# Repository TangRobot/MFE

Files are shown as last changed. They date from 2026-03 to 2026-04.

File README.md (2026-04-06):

# MFE: Multimodal Hand Exoskeleton

This is the official open-source repository for the paper:

**MFE: A Multimodal Hand Exoskeleton With Interactive Force, Pressure and Thermo-Haptic Feedback**

📄 [Read the Paper](http://arxiv.org/abs/2604.02820)

---

## Hardware

### Hand Exoskeleton (Canonical Version)

#### BOM

| Item | Specification | Quantity | Notes | Link |
|---|---|---|---|---|
| 3D Printed Parts | See `Hardware/Hand_Exoskeleton_CAD` | 1 set | Print each file once | - |
| Dynamixel Servos | XL-330-M288-T | 5 | with cables & screws | https://en.robotis.com/shop_en/item.php?it_id=902-0163-000 |
| U2D2 Hub | - | 1 | - | https://en.robotis.com/shop_en/item.php?it_id=902-0132-000 |
| U2D2 PHB Set | - | 1 | - | https://en.robotis.com/shop_en/item.php?it_id=902-0145-001 |
| DC Power Supply | 5V | 1 | - | - |
| Screws | M3 × 6 mm | 2 | - | - |
| Screws | M3 × 8 mm | 3 | - | - |
| Screws | M3 × 16 mm | 15 | - | - |
| Lock Nuts | M3 anti-slip | 15 | - | - |
| Heat-set Inserts | M3 × 3 mm (height) × 4.2 mm (OD) | 2 | - | - |
| EVA Foam | 10 cm × 10 cm | 1 | Recommended: 2 mm thickness, Shore hardness 30A | - |
| Velcro Straps (Wide) | 40 cm (length) × 20 mm (width) | 2 | For hand fixation | https://e.tb.cn/h.ih3Ne5haJRBw5nE?tk=OanP5ZXM8IF |
| Velcro Straps (Narrow) | 8 cm (length) × 5 mm (width) | Several | Optional for fingertip fixation | https://e.tb.cn/h.i6odaRXD7jrzqni?tk=6yex5ZX9u82 |

#### 3D Printing Requirements

To print all required parts, you will need:

- 3D printer (0.4 mm nozzle)
- PLA filament (1 spool)
- TPU 95A filament (1 spool)

### Assembly Instructions

0. Before starting the assembly process, configure all Dynamixel servos by assigning their IDs, setting the baud rate, and verifying that each servo operates correctly. Determine the correspondence between each servo and finger in advance.

1. Print all structural components from the directory `Hardware/Hand_Exoskeleton_CAD`, ensuring that you print each file once. For PLA parts, use at least four wall layers and 30% infill, and organize finger linkage components separately to avoid confusion. For TPU 95A parts, use 100% infill, and orient the fingertip sleeves so that the smaller opening faces the print bed.

2. Use a soldering iron to embed two heat-set inserts into the side holes of the lower base component.

3. Assemble the five finger linkages using M3 × 16 mm screws and M3 lock nuts, and adjust the screw tightness so that each joint rotates freely without resistance.

4. Attach the distal ends of each linkage to the servo horns using the longer screws provided in the Dynamixel kit.

5. Mount the servos and corresponding linkages onto the base structure as follows: attach the index and ring fingers to the upper base, attach the middle and little fingers to the lower base, and attach the thumb to the side base. Ensure correct ordering and alignment during installation.

6. Connect the servos in pairs using Dynamixel cables by pairing the index with the ring finger servos and the middle with the little finger servos.

7. Assemble the upper and lower base structures using M3 × 8 mm screws.

8. Attach the side base to the lower base using M3 × 6 mm screws.

9. Connect all servos using Dynamixel cables and link them to the U2D2 Hub.

10. Cut the EVA foam into an appropriate shape and attach it to the surface of the lower base that contacts the back of the hand.

11. Use wide Velcro straps to secure the exoskeleton onto the back of the hand.

12. Use narrow Velcro straps to further secure the fingertip sleeves if necessary.

---

## Software

### Installation

The Dynamixel SDK can be installed using the following command:

```bash
pip install dynamixel_sdk
```

### Usage

Please refer to the [Official Dynamixel SDK Documentation](https://emanual.robotis.com/docs/en/software/dynamixel/dynamixel_sdk/download/) and our [paper](http://arxiv.org/abs/2604.02820) for logic on reading encoder positions and setting force feedback intensity.

A simple implementation example is provided in `Software/MFE_control.py`, which demonstrates force feedback control between the hand exoskeleton and the Inspire RH56BFX robotic hand (both for right hand). Please follow the TODO comments to adapt it to your device, or extend this implementation to develop control logic for other robotic hands.

---

## Citation

If you use this repository in your research, please cite:

```bash
@ARTICLE{Tang2026MFE,
  author={Tang, Ziyuan and Guo, Yitian and Xiao, Chenxi},
  journal={IEEE Robotics and Automation Letters}, 
  title={MFE: A Multimodal Hand Exoskeleton With Interactive Force, Pressure and Thermo-Haptic Feedback}, 
  year={2026},
  volume={11},
  number={3},
  pages={3756-3763},
  doi={10.1109/LRA.2026.3662616}}
```

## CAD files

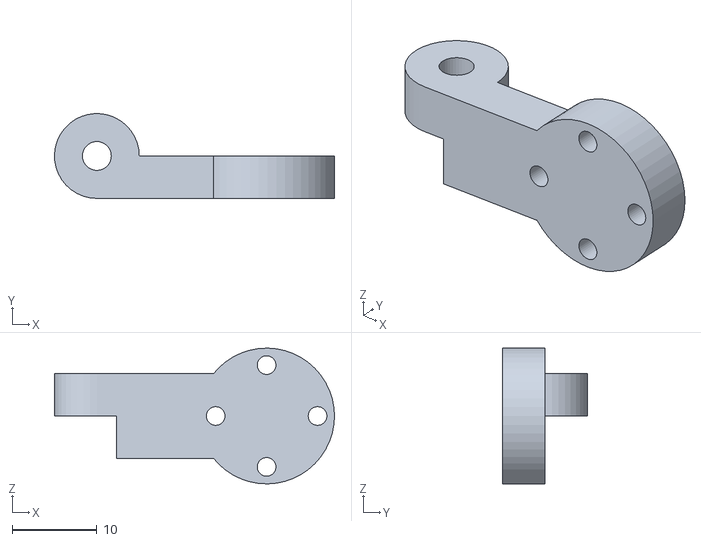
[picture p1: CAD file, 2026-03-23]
Hardware/Hand_Exoskeleton_CAD/PLA/middle_link3.STL
33.0 x 9.99 x 16.0

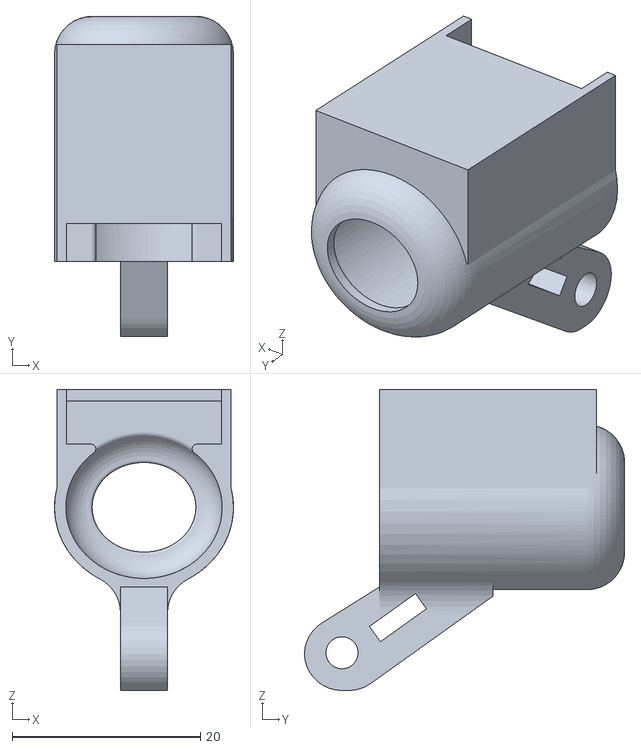
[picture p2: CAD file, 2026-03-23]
Hardware/Hand_Exoskeleton_CAD/TPU/index_sleeve.STL
19.0 x 34.0 x 31.9

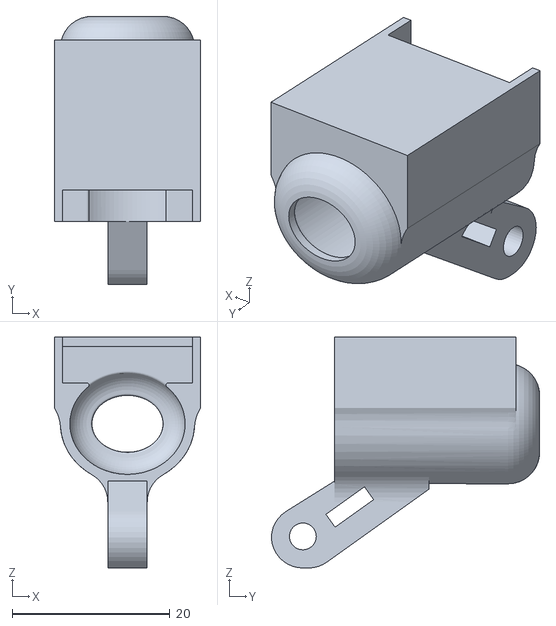
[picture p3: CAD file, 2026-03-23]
Hardware/Hand_Exoskeleton_CAD/TPU/little_sleeve.STL
18.5 x 34.0 x 29.3

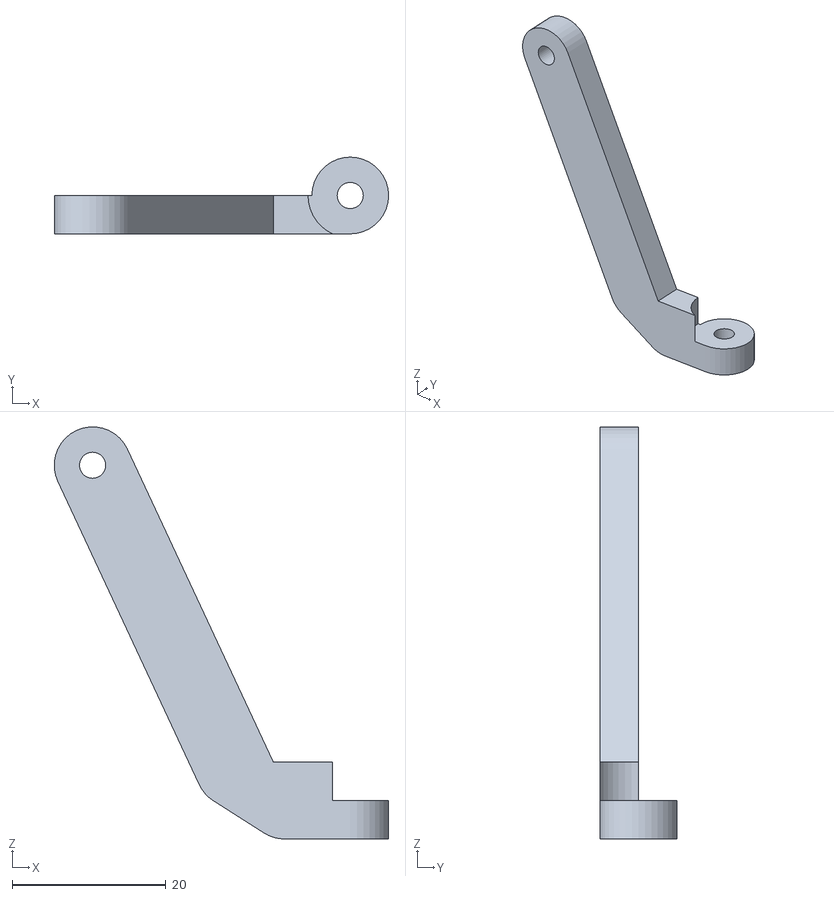
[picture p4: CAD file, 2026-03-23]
Hardware/Hand_Exoskeleton_CAD/PLA/thumb_link2.STL
43.5 x 10.0 x 53.7

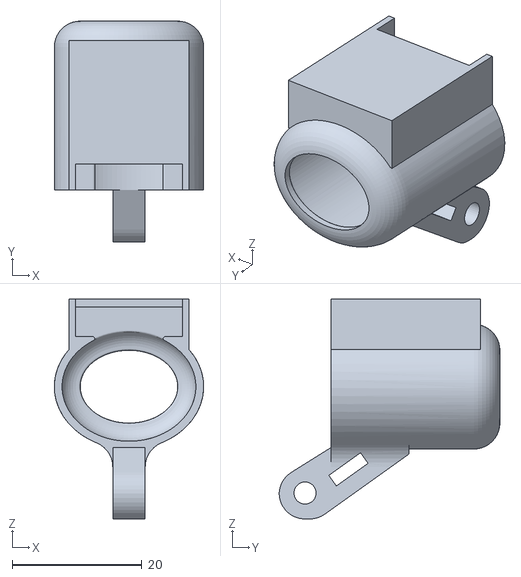
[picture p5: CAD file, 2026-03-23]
Hardware/Hand_Exoskeleton_CAD/TPU/thumb_sleeve.STL
23.0 x 34.0 x 33.9

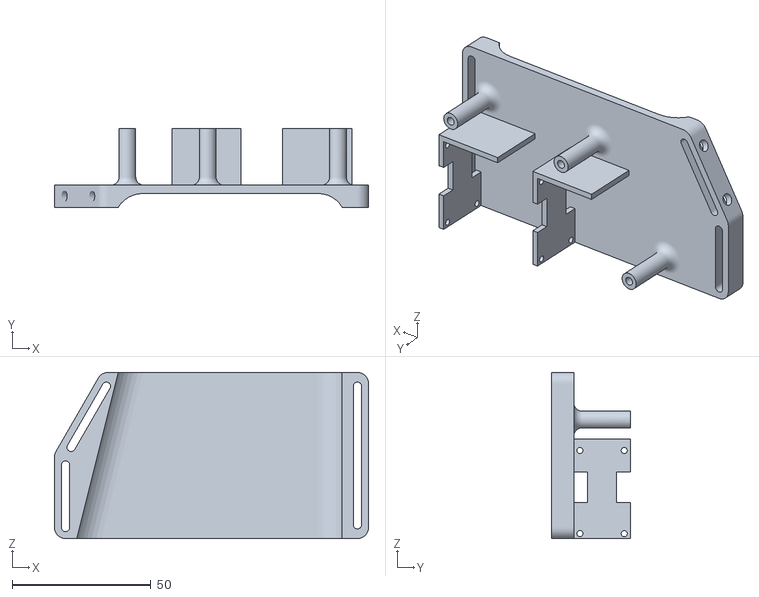
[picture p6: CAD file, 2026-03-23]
Hardware/Hand_Exoskeleton_CAD/PLA/lower_base.STL
113.3 x 28.4 x 60.0

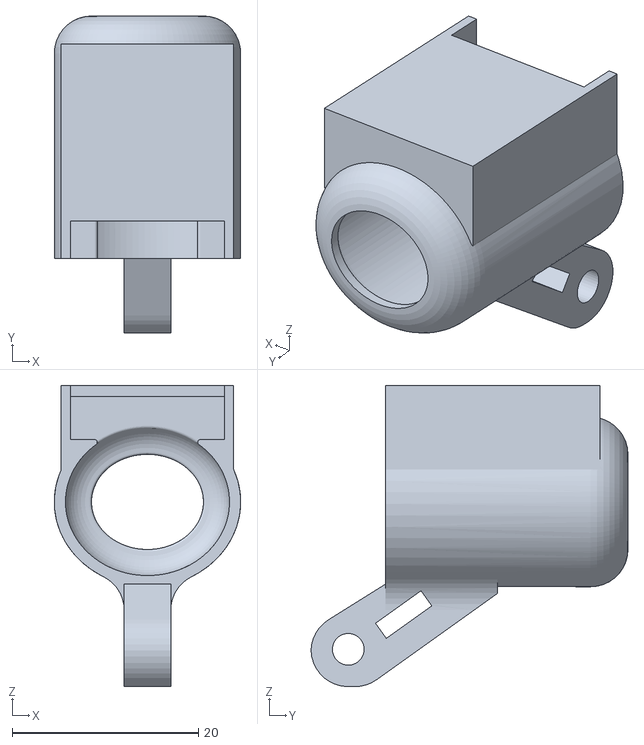
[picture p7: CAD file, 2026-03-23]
Hardware/Hand_Exoskeleton_CAD/TPU/middle_sleeve.STL
20.0 x 34.0 x 32.3

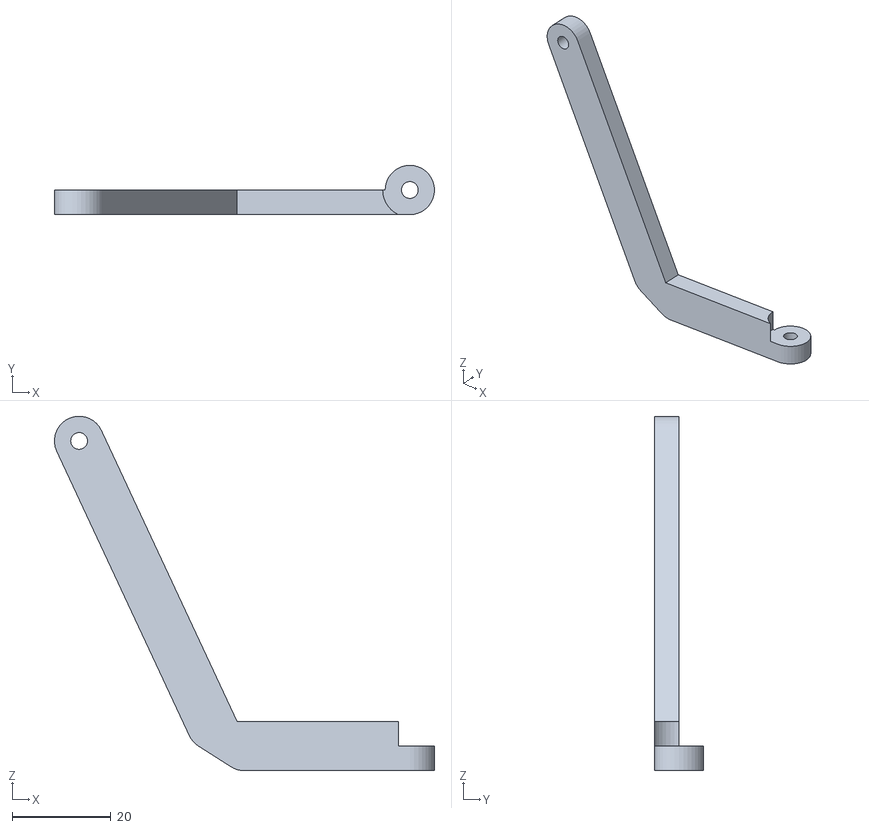
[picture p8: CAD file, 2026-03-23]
Hardware/Hand_Exoskeleton_CAD/PLA/middle_link2.STL
77.0 x 10.0 x 71.8

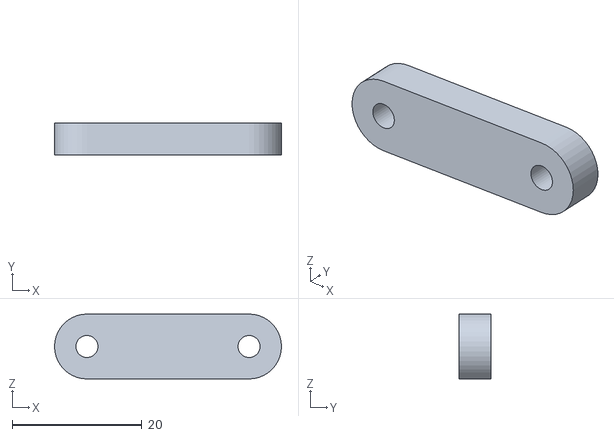
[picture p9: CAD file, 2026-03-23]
Hardware/Hand_Exoskeleton_CAD/PLA/thumb_link1.STL
35.0 x 5.00 x 10.0

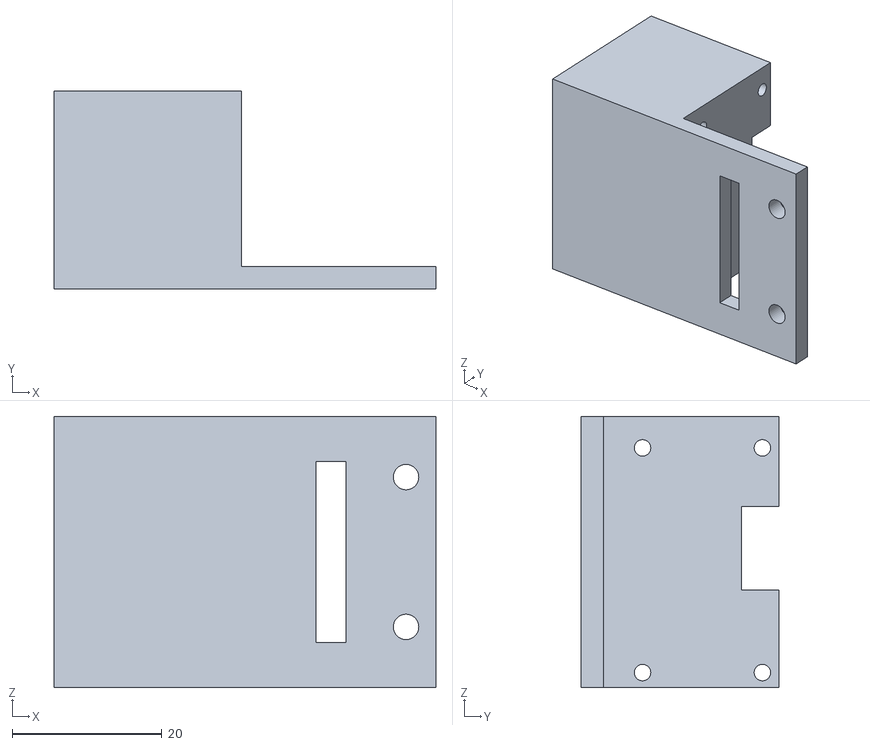
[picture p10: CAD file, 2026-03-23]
Hardware/Hand_Exoskeleton_CAD/PLA/side_base.STL
51.0 x 26.4 x 36.2

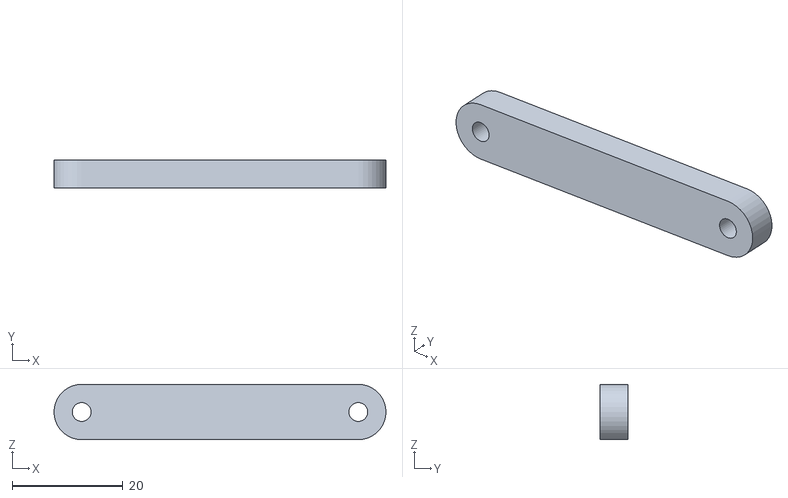
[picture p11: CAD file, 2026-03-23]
Hardware/Hand_Exoskeleton_CAD/PLA/ring_link1.STL
60.0 x 5.00 x 10.0

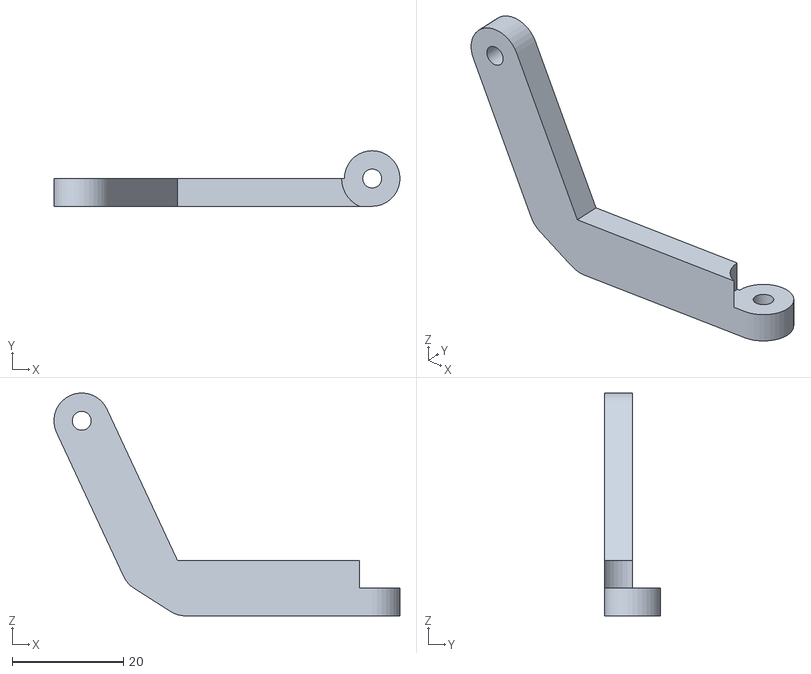
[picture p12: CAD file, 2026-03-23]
Hardware/Hand_Exoskeleton_CAD/PLA/little_link2.STL
62.2 x 10.0 x 40.1

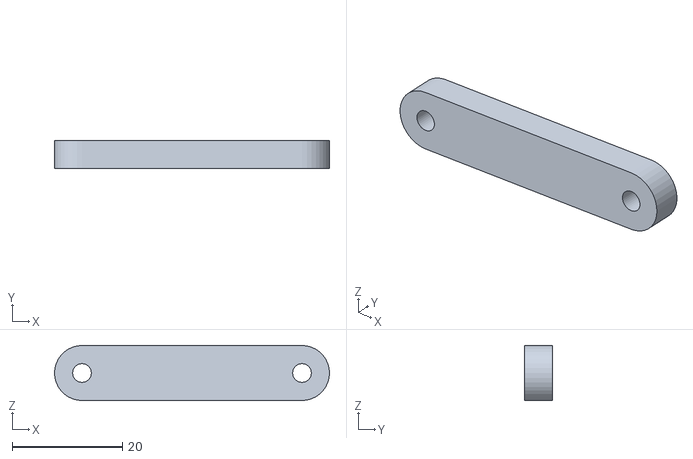
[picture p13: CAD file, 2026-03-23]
Hardware/Hand_Exoskeleton_CAD/PLA/little_link1.STL
50.0 x 5.00 x 10.0

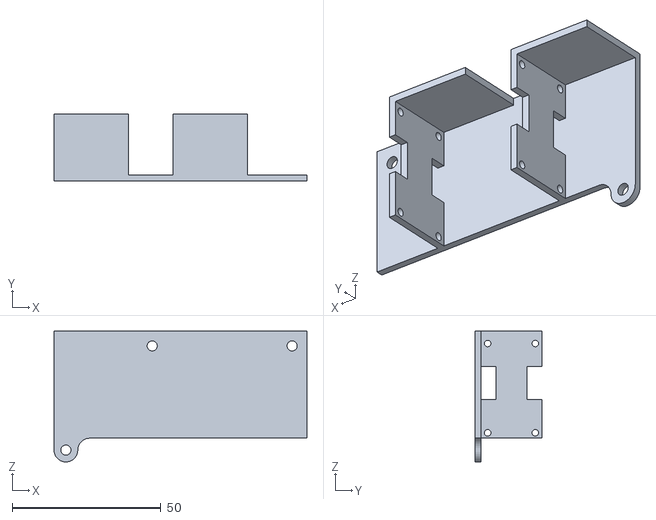
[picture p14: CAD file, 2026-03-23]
Hardware/Hand_Exoskeleton_CAD/PLA/upper_base.STL
85.0 x 22.4 x 44.0

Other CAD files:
Hardware/Hand_Exoskeleton_CAD/TPU/ring_sleeve.STL
Hardware/Hand_Exoskeleton_CAD/PLA/index_link1.STL
Hardware/Hand_Exoskeleton_CAD/PLA/index_link2.STL
Hardware/Hand_Exoskeleton_CAD/PLA/middle_link1.STL
Hardware/Hand_Exoskeleton_CAD/PLA/ring_link2.STL

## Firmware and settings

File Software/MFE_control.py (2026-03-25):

"""
This file is part of the official implementation for the paper:
"MFE: A Multimodal Hand Exoskeleton With Interactive Force, Pressure and Thermo-Haptic Feedback".
DOI: 10.1109/LRA.2026.3662616

This script provides basic functionalities for communicating with Hand Exoskeleton,
including state reading and control command execution, and serves as a reference
implementation for the force feedback control in the MFE system.

The code is intended as a minimal and adaptable example. Users should modify and
extend it according to their specific hardware setup and experimental requirements.

Please adapt this code to your own device by following the TODO comments in the file.
In particular, make sure to configure parameters such as:
- Serial port name
- Baud rate
- Servo IDs
- Control mode and limits
- Dex hand control logic

Refer to the official Dynamixel SDK documentation for detailed usage instructions.

If you use this code in your research, please cite the corresponding paper.

This project is released under the MIT License.
"""

import os
import numpy as np
from pymodbus import FramerType
from pymodbus.client import ModbusSerialClient
from dynamixel_sdk import *

# ------------------- Configuration Section -------------------

ADDR_TORQUE_ENABLE          = 64
ADDR_GOAL_POSITION          = 116
ADDR_PRESENT_POSITION       = 132
ADDR_DRIVE_MODE             = 11
ADDR_GOAL_CURRENT           = 102
TORQUE_ENABLE               = 1
TORQUE_DISABLE              = 0
DRIVE_MODE_CURRENT          = 0

# TODO: Configure these parameters according to your Dynamixel servo setup.
DXL_ID = [1, 2, 3, 4, 5] #From thumb to little finger.
DEVICENAME = 'COM1'
BAUDRATE = 115200
PROTOCOL_VERSION = 2.0
# TODO: Configure these parameters according to your Inspire hand setup,
# or implement your own hand control logic if you are using a different dex hand.
HAND_PORT = 'COM2'
HAND_BAUDRATE = 115200

# ------------------- Utility Functions -------------------

def getch():
    if os.name == 'nt':
        import msvcrt
        return msvcrt.getch().decode()
    else:
        import sys, tty, termios
        fd = sys.stdin.fileno()
        old_settings = termios.tcgetattr(fd)
        try:
            tty.setraw(fd)
            ch = sys.stdin.read(1)
        finally:
            termios.tcsetattr(fd, termios.TCSADRAIN, old_settings)
        return ch

def check(dxl_comm_result, dxl_error, packetHandler):
    if dxl_comm_result != COMM_SUCCESS:
        print(packetHandler.getTxRxResult(dxl_comm_result))
    elif dxl_error != 0:
        print(packetHandler.getRxPacketError(dxl_error))

# ------------------- Inspire Hand Control -------------------
# TODO: Implement your own hand control logic if you are using a different dex hand.
def create_modbus_client():
    client = ModbusSerialClient(
        framer=FramerType.RTU,
        port=HAND_PORT,
        baudrate=HAND_BAUDRATE,
        timeout=1,
        stopbits=1,
        bytesize=8,
        parity='N'
    )
    if not client.connect():
        raise RuntimeError('Unable to connect to Modbus RTU server.')
    return client

def write_single_register(client, hand_id, reg_addr, regval_int16):
    result = client.write_register(reg_addr, regval_int16, device_id=hand_id)
    return result.isError(), result

def write_multiple_registers(client, hand_id, reg_addr, values):
    result = client.write_registers(reg_addr, values, device_id=hand_id)
    return result.isError(), result

def read_register(client, hand_id, reg_addr, num_int16_regs=6, dtype=np.int16):
    result = client.read_holding_registers(reg_addr, count=num_int16_regs, device_id=hand_id)
    if result.isError():
        return []
    registers = result.registers
    results = []
    for val in registers:
        if dtype in (np.int16, np.uint16):
            results.append(np.array(val))
        elif dtype in (np.int8, np.uint8):
            results.append(np.array(val & 0xff))
            results.append(np.array((val >> 8) & 0xff))
        else:
            results.append(np.array(val))
    return np.array(results).astype(dtype)

class InspireHand:
    def __init__(self, client, hand_id):
        self.client = client
        self.hand_id = hand_id
    def set_pos(self, pos, index=None):
        if index is not None:
            if not 0 <= index <= 5:
                return False, 'Index out of range'
            reg_addr = 0x05C2 + index * 2
            return write_single_register(self.client, self.hand_id, reg_addr, pos)
        if len(pos) != 6:
            return False, None
        reg_addr = 0x05C2
        return write_multiple_registers(self.client, self.hand_id, reg_addr, pos)
    def set_force(self, force, index=None):
        if index is not None:
            if not 0 <= index <= 5:
                return False, 'Index out of range'
            reg_addr = 0x05DA + index * 2
            return write_single_register(self.client, self.hand_id, reg_addr, force)
        if len(force) != 6:
            return False, None
        reg_addr = 0x05DA
        return write_multiple_registers(self.client, self.hand_id, reg_addr, force)
    def read_force(self):
        reg_addr = 0x062E
        return read_register(self.client, self.hand_id, reg_addr, num_int16_regs=6)

# ------------------- Dynamixel Servo Control -------------------

def setup_dynamixel():
    portHandler = PortHandler(DEVICENAME)
    packetHandler = PacketHandler(PROTOCOL_VERSION)
    if not portHandler.openPort():
        raise RuntimeError('Failed to open the port')
    if not portHandler.setBaudRate(BAUDRATE):
        raise RuntimeError('Failed to set baudrate')
    return portHandler, packetHandler

# ------------------- Main Control Logic -------------------

def main():
    # Initialize hardware
    # TODO: Implement your own initialization logic if you are using a different dex hand.
    client = create_modbus_client()
    hand = InspireHand(client, hand_id=0x01)
    portHandler, packetHandler = setup_dynamixel()
    initial_position = [0] * 5
    longest_position = [0] * 5
    finger_position = [0] * 5
    goal_current = [0] * 5
    # Disable torque for all servos
    for i in DXL_ID:
        dxl_comm_result, dxl_error = packetHandler.write1ByteTxRx(portHandler, i, ADDR_TORQUE_ENABLE, TORQUE_DISABLE)
        check(dxl_comm_result, dxl_error, packetHandler)
    # Set initial positions based on user input
    print('Bend your thumb and press any key to set initial position.')
    getch()
    i = DXL_ID[0]
    longest_position[0], dxl_comm_result, dxl_error = packetHandler.read4ByteTxRx(portHandler, i, ADDR_PRESENT_POSITION)
    check(dxl_comm_result, dxl_error, packetHandler)
    print('Extend your thumb straight and press any key to set initial position.')
    getch()
    initial_position[0], dxl_comm_result, dxl_error = packetHandler.read4ByteTxRx(portHandler, i, ADDR_PRESENT_POSITION)
    check(dxl_comm_result, dxl_error, packetHandler)
    for cmd, val in [(ADDR_TORQUE_ENABLE, TORQUE_DISABLE), (ADDR_DRIVE_MODE, DRIVE_MODE_CURRENT), (ADDR_TORQUE_ENABLE, TORQUE_ENABLE)]:
        dxl_comm_result, dxl_error = packetHandler.write1ByteTxRx(portHandler, i, cmd, val)
        check(dxl_comm_result, dxl_error, packetHandler)
    print('Make a fist and press any key to set initial position.')
    getch()
    for idx, i in enumerate(DXL_ID[1:], 1):
        longest_position[idx], dxl_comm_result, dxl_error = packetHandler.read4ByteTxRx(portHandler, i, ADDR_PRESENT_POSITION)
        check(dxl_comm_result, dxl_error, packetHandler)
    print('Flat your hand and press any key to set initial position.')
    getch()
    for idx, i in enumerate(DXL_ID[1:], 1):
        initial_position[idx], dxl_comm_result, dxl_error = packetHandler.read4ByteTxRx(portHandler, i, ADDR_PRESENT_POSITION)
        check(dxl_comm_result, dxl_error, packetHandler)
        for cmd, val in [(ADDR_TORQUE_ENABLE, TORQUE_DISABLE), (ADDR_DRIVE_MODE, DRIVE_MODE_CURRENT), (ADDR_TORQUE_ENABLE, TORQUE_ENABLE)]:
            dxl_comm_result, dxl_error = packetHandler.write1ByteTxRx(portHandler, i, cmd, val)
            check(dxl_comm_result, dxl_error, packetHandler)
        dxl_comm_result, dxl_error = packetHandler.write2ByteTxRx(portHandler, i, ADDR_GOAL_CURRENT, 0)
        check(dxl_comm_result, dxl_error, packetHandler)
    # Main control loop
    print('Press any key to continue! (or press ESC to quit!)')
    if getch() == chr(0x1b):
        return
    while True:
        # Read force from Inspire hand
        # TODO: Implement your own read force logic if you are using a different dex hand.
        present_force = hand.read_force()
        for idx, i in enumerate(DXL_ID):
            # Read present positions from Dynamixel servos and compute control commands
            present_position, dxl_comm_result, dxl_error = packetHandler.read4ByteTxRx(portHandler, i, ADDR_PRESENT_POSITION)
            if present_position - initial_position[idx] >= 0:
                finger_position[idx] = int((present_position - initial_position[idx]) * 2000 // abs(longest_position[idx] - initial_position[idx]))
            else:
                finger_position[idx] = 0
            finger_position[idx] = min(finger_position[idx], 2000)
            # Compute goal current based on the force feedback from the Inspire hand
            force = present_force[4 - idx]
            goal_current[idx] = 0 if force <= 150 else max(-int(force / 6), -1749)
            # Send force feedback commands to Dynamixel servos
            dxl_comm_result, dxl_error = packetHandler.write2ByteTxRx(portHandler, i, ADDR_GOAL_CURRENT, goal_current[idx])
        # Send position commands to the Inspire hand
        # TODO: Implement your own position control logic if you are using a different dex hand.
        finger_position[0] = min(finger_position[0], 1200)
        hand.set_pos([finger_position[4], finger_position[3], finger_position[2], finger_position[1], finger_position[0], 1750])
        hand.set_force([1000] * 6)

if __name__ == '__main__':
    main()
